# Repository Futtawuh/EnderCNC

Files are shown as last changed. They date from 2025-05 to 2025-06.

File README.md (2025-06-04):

# EnderCNC's!

### Got too many Enders laying around? Dont need a [5th Trident?](https://github.com/yell3D/Ender3dent) Well! Try one of the EnderCNC's, born from a lack of sleep, a wish to learn more CAD and too many spare parts floating around.

## Current plan has changed a bit. There will be multiple versions of these.

### A [new cheaper version](https://github.com/Futtawuh/EnderCNCs/tree/main/Ender3CNC) is now released!

- Based only on the Ender 3 PRO, where every part from the printer counts to keep the BOM cost very low. This will now be the Ender3CNC.
- As of now BOM cost is ~60$ not counting the Ender 3 PRO or dremel/spindle. But chances are you have some of the BOM laying around already.
- This version will include CAD for milling its own aluminium upgrades if it can handle it like the original version. 



BOM and CAD will be released into "BETA" when CAD is "finished".

- The [original EnderCNC](https://github.com/Futtawuh/EnderCNCs/tree/main/EnderCNC%20CAD) underwent a facelift and is tested OK on parts and is now in "release" version and wont have updates unless issues arise. (this was loosely based on the Ender 3 PRO + Ender 4 parts)


### Other versions

- The MGN version will be based around the new Ender3CNC version, with minor tweaks to the frame layout resulting in a bigger cutting area.
- Mill style (MILO CNC) is also being worked on but might not be built unless i find more cheap Ender's. 

# Always check out the [Changelog](https://github.com/Futtawuh/EnderCNC/blob/main/Changelog.md) for any updates done to the CADs. 

Here are some videos from the original EnderCNC pre facelift using a 150W 20$ dremel.  

https://github.com/user-attachments/assets/92859aa1-7ed4-4385-81ab-ec51dbf1d837

https://github.com/user-attachments/assets/d6dc1093-e1e1-4dbe-b1f9-021c9d8749b4

# (Residue on the bit is just sticky-tape from doing the holes)

https://github.com/user-attachments/assets/a4f48e41-3836-4eb9-8406-88c55c8b1824

part

120mm bed carriage milled on EnderCNC for a 120mm cubed Voron SW. 


# Discord: ravenkeeper

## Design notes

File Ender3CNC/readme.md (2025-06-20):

# Ender 3 PRO based CNC!


## Fully built!
https://github.com/user-attachments/assets/6816d12f-9653-461b-ad77-0ac71268e209

Print settings I used: PLA+, 5 wall, 5 top, 5 bottom, 40% gyroid.

## My setup:

Im just running the original MCU with Klipper for the control and Fusion360 for CAM (free version) with a klipperized post processor. So far no real issues. You might want to swap to a board with TMC control (skr pico/micro4) if you realy want to push it.  Im using an old laptop with Ubuntu with klipper on as a substitute for a Raspberry pi. 

You can ofcourse go the GRBL route if you want. I just wanted to use klipper since people coming from 3D printers are somewhat familiar with that.

## Check out the ["Build guide"](https://github.com/Futtawuh/EnderCNCs/blob/main/Ender3CNC/Manual.md) (not finished) 

- Reusing as much as possible from the Ender 3 PRO down to the screws.
- Cheaper BOM than the original EnderCNC. BOM is mostly just some screws, 2x linear rails for Z and m3/m5 tnuts.
- Easy to scale up or down to any size if not using Ender 3 Pro frame. 

### reusing:
* Frame
* steppers
* wires (might need to extend some)
* leadscrew
* leadscrew nut
* coupler
* mcu
* psu
* most of the nuts and bolts
* vwheels
* alu spacers
* screen if you want



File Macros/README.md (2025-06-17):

# E3CNC Macros for Workspace XYZ0 Positioning

## What These Macros Do and Why

These macros are designed to **manually set the workspace XYZ0** for basic milling tasks.

When you press a `ZERO` macro, the machine’s current position is saved into a **variables file**. This acts as a backup in case of:

- MCU failure
- Emergency Stop (E-stop) had to be pressed
- Firmware reset or crash

This removes the need to manually record XYZ coordinates before zeroing — everything is saved automatically!

---

## Failed Mid-Job? Firmware Restarted?

>  **Note:** This recovery method only works if you’re using the same workpiece and want to **resume** the job.

### Scenario:
Your job is running, and the MCU crashes, causing a firmware restart.  
Follow these steps to recover:

1. Press the `LOAD_OFFSETS` macro.
    - This will re-home the CNC and move it to the **last saved machine position**.
2. Press the `ZERO_ALL` macro.
    - This re-applies your previous workspace XYZ0.
3. Restart the original job.
    - If you're lucky, this might **save the workpiece** from becoming scrap!

---

## Manual Workpiece ZERO Position Setup

>  **Make sure the Dremel/Spindle is NOT spinning during setup!**

---

### Step-by-Step Guide Manual ZERO:

1. Attach the workpiece securely.
2. Home the CNC machine.
3. Move the CNC via Mainsail to position the bit roughly at the center of the workpiece.
4. Lower the Z-axis until the bit is about **1mm above** the workpiece.
5. Place a **thin sheet of paper** under the bit and slowly lower the Z-axis:
    - Stop when the bit **grabs the paper slightly** (you feel friction).
    - Press the `ZERO_Z` macro — this sets Z0.
6. Raise Z by **2–3mm** to avoid crashing into the workpiece if it’s not perfectly flat.
7. Move the CNC using XY controls to the corner you've defined as the origin in Fusion/CAM.
8. Press `ZERO_X` and `ZERO_Y` macros.
    - ✅ X and Y are now set to workpiece XY0.
    - ❌ Do **not** press `ZERO_Z` again.
9. Start your job from Mainsail.

> **Use PPE, dont crash and stay safe.**

---

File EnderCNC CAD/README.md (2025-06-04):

Cheaper version? - > ["E3CNC"](https://github.com/Futtawuh/EnderCNCs/tree/main/Ender3CNC)

# CAD file for the original EnderCNC

- Loosely based on the Ender 3 pro + Ender 4 with some extras. 
- Made to use up my old spare parts.

https://github.com/user-attachments/assets/380edf0b-43fd-45f2-9f59-4e6d6528cb2b





Here are some videos from the original EnderCNC pre facelift using a 150W 20$ dremel.  

https://github.com/user-attachments/assets/92859aa1-7ed4-4385-81ab-ec51dbf1d837

https://github.com/user-attachments/assets/d6dc1093-e1e1-4dbe-b1f9-021c9d8749b4

# (Residue on the bit is just sticky-tape from doing the holes)

https://github.com/user-attachments/assets/a4f48e41-3836-4eb9-8406-88c55c8b1824

part

120mm bed carriage milled on EnderCNC for a 120mm cubed Voron SW. 


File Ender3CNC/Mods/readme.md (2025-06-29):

# 20mm extended front corners MOD.
- These add 20mm cutting area to the Y axis, with "halflapped" blindjoints like the back corners. 



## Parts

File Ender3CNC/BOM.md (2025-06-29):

# This is just a reference BOM from my own build and CAD. I might have counted wrong. If you find any issues please let me know. 

## I've tried to keep the BOM parts as close as possible to a Voron 3d Printer build in hopes people already have some of the BOM already.

# Screws from Ender 3 Pro

- 2x m5x30 button head from e3p z axis vwheel holder.  [ENDER3]
- 16x M5x45 bolts from the e3p frame (remove the shims if you can) [ENDER3]
- 2x M4x20  [ENDER3]
- 2x M4x16  [ENDER3]
- 6x M3x10  [ENDER3]
- 4x M3x40  [ENDER3]
- All M5 nuts [ENDER3]
- 4x M5x8 [ENDER3]
- 12x M3x6 [ENDER3]
- 2x M4x10 + 2x M4 t-nut [ENDER3]
- 11x m3x10  [ENDER3]
- 2x 688 bearings if yours have these, if not buy 608zz as listed in BOM
- M5x30 screws

# BUY:

- 3x ~500mm lenght belts, best to just buy a 3-5 meter roll on Ali for cheap. 6mm GT2 
- 2x 608ZZ bearings (8x22x7) [or check if your ender 3 X axis tensioner got 2x 688 bearings]
- 4x D2F-L Microswitch (limitswitch) (Ender only has 3, but just get a 10 pack for cheap on Ali for an easier time fitting them in place)
- ~20x m3 Tnuts (2020) [Can use sliding or t-nuts]
- ~40x M5 Tnuts (2020) [Can use sliding or t-nuts]
- 10x m5 locknuts (hexnuts)
- 30x m3 "voron spec" heat insets - m3x4x5
- ~70x M5x16 BHscrew
- 2x 150mm MGN12H (1 carriage pr rail)
- 1x M5x65 screw [middle lower X axis wheel, can be optoinal as i have no idea if it actually does anything. More=Better?]
- 3x 20t, 6mm Width, 5mm bore pulleys GT2
- 4x M5 shims (od10 - id5 - 1mm thick)
- 22x M3x10 screws (not countersunk)

# Optional:

- 8x 5mmID x 8mmOD x 8mm length alu spares for Y axis wheels. (replaces printed spacers)

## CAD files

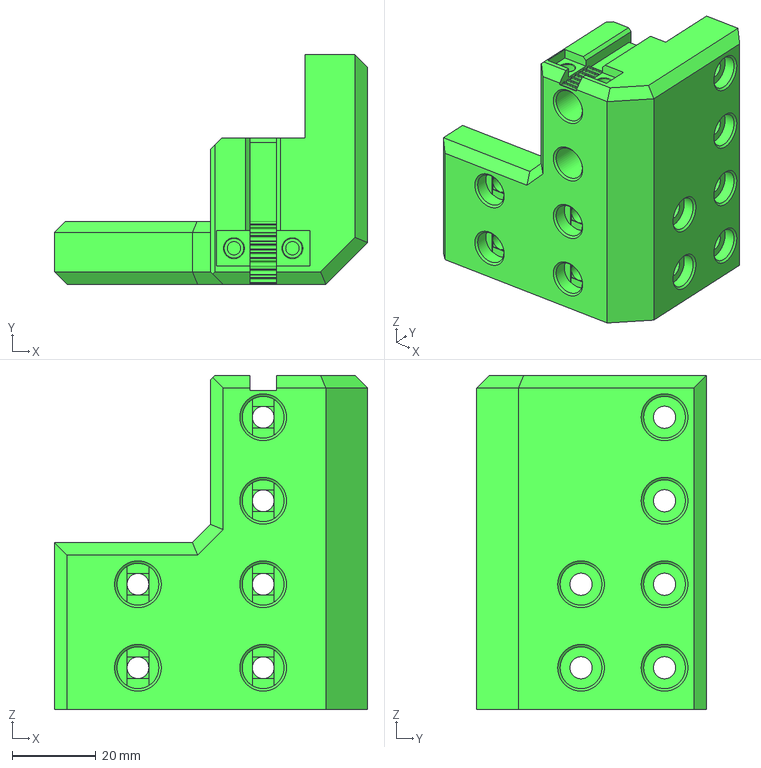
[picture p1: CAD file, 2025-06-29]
Ender3CNC/Mods/[MOD] 20mm extended front-R.step
75.0 x 55.0 x 80.0 mm

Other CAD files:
Ender3CNC/Mods/[MOD] 20mm extended front-L.step
Ender3CNC/Mods/[MOD] 20mm extended front-L.stl
Ender3CNC/Mods/[MOD] 20mm extended front-R.stl

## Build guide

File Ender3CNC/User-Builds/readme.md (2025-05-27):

# Builds from other users! 

### Beta tester build by Steve! Serial E3CNC.01


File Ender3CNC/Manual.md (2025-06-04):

# Ender 3 PRO based CNC Build manual (not finished)

### !! Note: This "guide" might contain errors with hardware parts, if you find any issue please let me know !!

## Things you'll need. 
- Ender 3 PRO (not the non pro version)
- M5 tap
- Ability to cut Alu extrusions to length.
- Hexdrives
- RaspberryPi or old laptop running linux/klipper. (if you want to use klipper)
- Dremel/Spindle of your choice (You might have to adjust the dremel clamps to fit yours)
- Printed pressfit pulley extraction tool (this can be tricky, but you can also cut the off if you want)

### Print settings I used: PLA+, 5 wall, 5 top, 5 bottom, 40% gyroid.

## Bearing Choice
### If you dont have 608Z use the F688Z from the Ender 3 Pro X axis tensioner. 
bearing_choice

## M3 Heatsets ( M3x5x4 "Voron spec") 

### X-Motor plate


### Corner Brackets
corner_heatsets

### XZ Carriage Plate
XZ_gantry_heatsets

### Dremel Plate
dremel_plate_heatset

### Z Carriage
Z_carriage_heatsets

### XY Joints 
XY_joints_heatsets

## M5 Locknuts - These should be pressfits!

### Z Carriage 
pressfit m5 hexnuts

### XZ Carriage Plate
xz_plate_pressfit m5 hexnuts

## Blind Joints

### Front 
blind joint front

### Back
* Should be offset by 20mm to gain more Y axis travel.
  
blind joint back

### What is this part? 
* This is the "X Endstop Buffer". It attaches to the X motor plate on the X endstop side to a heatinset.
* This "buffer" is needed if you are homing with the vacuum attachment or "splashguards" on to not collide in the Y extrusion.
* You will not need this attached if you are not using the vacuum attachment.
* M3x8/10 screw




# The build! 

### DO NOT PRESS IN THE ENDSTOPS AT ANY POINT UNTILL YOU START WIRING! YOU MIGHT NOT GET THEM OUT AGAIN AS THEY ARE PRESSFITS. 

## Frame
| Qty  | Item | Source  | Notes |
|---|---|---|---|
| 48pc | M5x16 BHSC | BUY | |
| 4pc  | M5x40 | Ender3  | |
| 4pc  | M5x8 | Ender3  | |
| 4pc  | M5 1mm Shims | BUY | |
| 52pc | M5 T-nuts | BUY | |

* DO NOT PRESS IN THE ENDSTOPS YET.
* Assemble frame as shown, take note of blind joints and 20mm offset on the back extrusion and check for square.
  - I found it easier to get a square frame on a known flat surface by adding the XY joints after the frame is built. Its a bit tricky, but very doable.

assable_frame

## XY joints
| Qty  | Item | Source | Notes |
|---|---|---|---|
| 8pc  | M5x45 SHSC | Ender3 | Remove the shims from these |
| 8pc  | M3x10 | BUY | |
| 8pc  | 8mm Spacer (Printed or 5mm bore Alu) | BUY | Do not use the aluminum spacers from the Ender3 here  |

* DO NOT PRESS IN THE ENDSTOP YET.
* Loosely attach the 20T pylleys.
* Assemble XY joints as shown WITHOUT the endstop.



## Mount XY joints to the frame. 
| Qty  | Item | Source | Notes |
|---|---|---|---|
| 8pc  | V-Wheels | Ender3 | |
| 8pc  | M5 Locknuts  | Ender3 or BUY  | |

* DO NOT PRESS IN THE ENDSTOP YET.
  - I slid the xy joint on while the frame was built.
  - Put on the 2 bottom wheels and loosely add M5 nut to them.
  - Place the bottom wheels in the V slot, hold it at a slight angle.
  - Add the 2 top wheels to the Vslot and angle up the XY joint with a slight wiggle the top screws should pop in the wheels.
  - Bit tricky but doable. Or if you want to just take of the 2040 from the frame and slide them on. Might need to re-square the frame though.
* After mounting both XY joints, doublecheck the measurement between the X extrusion mounting points before cutting the X extrusion.
* Ender 3 frames might not be 100% the same. so yours might be +- from 300mm.
* After cutting the X extrusion to size you need to tap 4 new m5 threads on the cut side.

x_beam

## Assemble X+Z Carriage
| Qty | Item | Source | Notes |
|---|---|---|---|
| 4pc | M3x8 BHSC | Ender3 | |
| 2pc | M3x10 | BUY | |
| 10pc  | M5x16 BHSC | BUY | |
| 2pc | M5x8 BHSC | Ender3 | |
| 4pc | M3x40 | Ender3 | |
| 4pc | M5x45 SHCH | Ender3 | Remove the shims |
| 1pc | M5x65 BHSC | BUY | |
| 12pc  | M3x8 SHSC | BUY | |
| 2pc | M3x16 BHSC | Ender3 | |
| 9pc | Alu Spacers | Ender3 | |
| 1pc | 28.35mm Printed Spacer  | Printed  | |
| 5pc | V-wheels | Ender3 | |
| 4pc | 32.60 mm spacer | Printed  | |
| 8pc | M3x10 BHSC | Ender3 | |

* DO NOT PRESS IN THE ENDSTOP YET.
* Cut Ender3 2020 extrusions to 150mm x2 pieces.
* Tap m5 threads in both ends of the 150mm 2020 extrusions.
* Press in bearings if you didnt already.
* Loosely attach the coupler to the Z motor.
* Loosely attach the 20T pulley to the X motor. 
* Attach both Z and X motors to their plates before continuing.
* Attach the 2020 extrusions as square and paralell as you can.
* Mount the X motor carriage to the ZX carriage with the wheels and spacers.
  - This can be a bit tricky, but doable after picking up the wheels and spacers from the floor a few times, sorry.
  - NOTE! Alu spacers from the Ender 3 are 8.35mm long, if you use 8mm long spacers from another source please use this [add part link here] printed spacer part for the lower middle wheel.
* Attach the Z bottom bearing plate and Z motor plate.
* Attach the MGN12 rails with the MGN12H carriages to the 2020 extrusions. (use a printed MGN12->2020 tool to get good alignment on the rails. Printables, Thingiverse etc)
  - NOTE! If you cut the 2020 a bit shorter than 150mm or the rails you ordered/cut are over 150mm dont worry, in the Z motor plate there are cutouts for the MGN rails to slide into if they are too long (max 4mm clearance)
* Attach the Z leadscrew nut to the Z carriage.
* Mount the Z carriage to the MGN12H carriages. - After mounting the Z carrige to the rails, slide it up and down to check for any binding in the rails, adjust rails if needed.
* Cut leadscrew to size. ~180mm but doublecheck with your setup. it should just about poke out of the lower Z bearing.  
* Screw in the leadscrew from the bottom bearing all the way to the Z motor coupler and secure it.
* Slide the assembly on the X extrusion that was cut to size. 






## Attach the X+Z assembly to the XY joint.
| Qty  | Item | Source  | Notes |
|---|---|---|---|
| 8pc  | M5x30 BHSC | Ender3  | |
| 4pc  | M5x16 BHSC | BUY | |



## Run the belts
| Qty  | Item | Source  | Notes |
|---|---|---|---|
| 3pc  | ~500mm GT2 6mm Belt | BUY | Control measure before cutting to length!! |
| 12pc | M3x10 | BUY | Migth be some spares from the Ender3 |
| 6pc  | Printed Belt Clamp | Printed | |



# TO BE CONTINUED

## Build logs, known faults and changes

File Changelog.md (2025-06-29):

# 29.06.2025
- Basic BOM listed. Please note that i might have not counted correclty. If you find any issues please let me know. BOM [here](https://github.com/Futtawuh/EnderCNCs/blob/main/Ender3CNC/BOM.md)
- Added optional front corners, adding 20mm extra Y cutting area. No changes to BOM.
- These are not added to the main CAD yet. But you can find them [here](https://github.com/Futtawuh/EnderCNCs/tree/main/Ender3CNC/Mods)
- Thanks Shadowphyre for the suggestion!

# 18.06.2025
- Macros for XYZ-0 positioning uploaded. 
- Tested out vac attachment, seems to do its job on wood, will test more on different materials. 

# 14.06.2025
- Had to wait for a new dremel as my new one was DOA. It arrived today, furter testing and cutting videos will be uploaded shortly!
- Will be testing differnt kinds of wood, some types of Plexi/acrylic and ofcourse some unknow grade aluminium. 

# 04.06.2025

### Ender3pro-CNC CAD uploaded!
- Fully built by me and a "beta" tester. Everything should fit nicely and easy enough to assemble!
- Build guide still not 100% finished, but it should give most pointers that you need
- Build guide and CAD is found ["HERE!"](https://github.com/Futtawuh/EnderCNCs/tree/main/Ender3CNC)
- If you need .step contact me on Discord: ravenkeeper (filesize too big to upload)

# 05.05.2025

### There will be multiple versions as time goes on. 
- Facelift version of the EnderCNC is in "release" stage, CAD wont be updated unless issues arise during use. 
- New Ender3CNC version soon in "BETA". Base 99% on the Ender 3 PRO. Cheaper alternative on vwheels etc.

Picture of the new version.


# 28.04.25

Facelift version built, will do minor tweaking to CAD, but everything fits like it should. New CAD will be uploaded soon.

# 26.03.25

* Uploaded facelift version CAD. This version is tested OK, does alu with a dremel pretty nicely if you know how to tune your DOC, feeds and speeds. 



# 20.03.25

* Udated CAD file. Added new look to the XY joints as the original was kinda lacking in the looks department. Added both dual bearing and single bearing version. (if you want the original one they are also in the CAD) 
 

* Relocated the X endstop to be in-set into the LEFT XY joint.
- (Wires coming out on the other side where the wire loom connects to the XY joint)
 

* Comparison old vs new.
 

# 19.03.25

* Added belt tension system for the Y belts on the Y motor carriages.
 

* Added "splash-guards" to limit debris from spilling over to the Y axis belts and rods. ( need to cut them in half in slicer unless you have a 400mm printer )
 
 

* Maktia 700 series ( or other Ø65mm spindle ) clamp added.
 

* Remixed Z carriage for more Z travel. But you'll have to cut the teethed part off a 8mmID 20t pulley, or use another 8mmID locking nut on the Z leadscrew. (lower 20t pulley cut to size on picture below)



* Bigger holes for ziptie cable management.
* Several fixes to the XY joints:
  - Fixed so the X carriage cant home over the Y extrusion.
  - Shorter screws for the Y belt clamps.
  - Longer XY joints with 55mm + 29mm LM bearings for more stability (optional)
  - You can now use either LMK10LUU or LMK10LUU + LM10UU for the XY joints. Using LMK+LMU does not reduce cutting area.

# 02.01.25

* Added 8mm rod mod CAD, using 8mm rods and 2x LMU8 bearings on each side for stiffness. (45mm long x2)

# 22.12.24

* Updated CAD with most of the hardware. Still a little bit left.
* Updated CAD X travel/limit switch for Z to not crash into Y extrusion if X homing without Z homed first. 

# 21.12.24

* Create Github
* Added CAD files
* Added DXF / PDF file of x gantry back plate.

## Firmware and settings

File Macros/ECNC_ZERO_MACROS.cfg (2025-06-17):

# E3CNC macros for workspace XYZ0 positioning

# What the macros do and why: 
#---------------------------------------------
# These macros are to manually set the workspace XYZ0 for any basic milling.
# When you use a "ZERO" macro, it saves your machines "original" position into a variables file. 
# This was done in case of MCU failure, E-stop needs to be pressed or any other reason for the machine to need a firmware reset.
# This removes the need to take notes of the XYZ position before hitting ZERO macros. 


# ! FAILED MID JOB AND FIRMWARE IS RESTARTED !
# NOTE! The following scenario will only work as long as you dont swap out the workpiece for a new one, wanting to try and save the failed job.  
# Scenario: You are in the middle of the job and the MCU crashes, causing a firmware restart. After a firmware restart, you can simply press the "LOAD_OFFSETS" macro
# and the machine will re-home, and go to its last originally saved machine position. From here you can simply press the "ZERO_ALL" macro and the machine sets the workspace XYZ0 to where it was before. 
# You can now restart the original job and might just save your workpiece from being scraps. 

# My manual workpiece ZERO position setup:
# !MAKE SURE THE DREMEL/SPINDLE IS NOT SPINNING!
#-------------------------------------------------
# 1. Attach the workpiece
# 2. Home the CNC
# 3. Move the CNC via mainsail until the bit is ~ at the center of the workpiece.
# 4. Move Z down until ~1mm above the workpiece. 
# 5. Take a thin piece of paper under the bit, move it back and forth while lowering Z, when the bit bites 
# the paper(slight friction), click ZERO_Z macro. Z is now at workpiece Z0.
# 6. Move Z up ~2-3mm or more to avoid crashing if the workpiece is not flat. 
# 7. Move the CNC from mainsail using XY movement to be above the corner you set as origin point in Fusion/CAM.
# 8. Click the ZERO_X and ZERO_Y macro. X and Y is now at workpiece XY0. (dont do Z macro as you already did that)
# 9. Start the job as normal from mainsail. Dont crash, use PPE and be safe.   

[gcode_macro ZERO_X] # Sets workspace X0 position.
gcode: 
  SAVE_VARIABLE VARIABLE=x_offset VALUE={printer.gcode_move.position.x}
  RESPOND PREFIX="info" MSG="Saved X Offset - X={printer.gcode_move.position.x}"
  SET_KINEMATIC_POSITION X=0

[gcode_macro ZERO_Y] # Sets workspace Y0 position.
gcode: 
  SAVE_VARIABLE VARIABLE=y_offset VALUE={printer.gcode_move.position.y}
  RESPOND PREFIX="info" MSG="Saved Y Offset - Y={printer.gcode_move.position.y}"
  SET_KINEMATIC_POSITION Y=0

[gcode_macro ZERO_Z] # Sets workspace Z0 position.
gcode: 
  SAVE_VARIABLE VARIABLE=z_offset VALUE={printer.gcode_move.position.z}
  RESPOND PREFIX="info" MSG="Saved Z Offset - Z={printer.gcode_move.position.z}"
  SET_KINEMATIC_POSITION Z=0

[gcode_macro ZERO_ALL] # Sets workspace XYZ0 position. 
gcode:
  SAVE_VARIABLE VARIABLE=z_offset VALUE={printer.gcode_move.position.z}
  RESPOND PREFIX="info" MSG="Saved Z Offset - Z={printer.gcode_move.position.z}"
  SET_KINEMATIC_POSITION Z=0
  SAVE_VARIABLE VARIABLE=y_offset VALUE={printer.gcode_move.position.y}
  RESPOND PREFIX="info" MSG="Saved Y Offset - Y={printer.gcode_move.position.y}"
  SET_KINEMATIC_POSITION Y=0
  SAVE_VARIABLE VARIABLE=x_offset VALUE={printer.gcode_move.position.x}
  RESPOND PREFIX="info" MSG="Saved X Offset - X={printer.gcode_move.position.x}"
  SET_KINEMATIC_POSITION X=0


[gcode_macro LOAD_OFFSETS] # Homes the machine and goes back to the last coords where XYZ0 was set. 
gcode:
  G28
  {% set svv = printer.save_variables.variables %}
  G1 F3000 X{svv.x_offset} Y{svv.y_offset} Z{svv.z_offset}
 
  RESPOND PREFIX="warn" MSG="Loaded offsets, going to: X={svv.x_offset} Y={svv.y_offset} Z={svv.z_offset}"


[gcode_macro CHECK_OFFSET_XYZ] # Checks what coords are saved and prints them in console. (no movement)
gcode:
  {% set svv = printer.save_variables.variables %}
  RESPOND PREFIX="info" MSG="Current Saved Offset - X={svv.x_offset} Y={svv.y_offset} Z={svv.z_offset}"

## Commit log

2024-12-22 Add files via upload
    Updates to CAD
2025-01-02 Add files via upload
    8mm rod mod, 2x LMU8 each side
2025-03-19 Rename E3-CNC BETA.step to dont use, outdated.step
    [dont use, outdated.step]
2025-05-04 Create EnderCNC CAD
